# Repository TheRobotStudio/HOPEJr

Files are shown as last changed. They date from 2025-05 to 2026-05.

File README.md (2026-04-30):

# HOPEJr

## Repository Structure

### 📁 [`Humanoid/`](./Humanoid/) - Full Humanoid Development
*Original work by Rob Knight and updates for new motors, Robstride 02*

This directory contains the comprehensive humanoid robot development including:
- **Complete Body Design**: Full humanoid with arms, torso, and leg structures
- **URDF Models**: Complete robot descriptions for simulation

### 📁 [`Arm/`](./Arm/) - Hugging Face Integration & Teleoperation
*Latest work by Martino Russi at Hugging Face*

This directory contains the most recent development focused on:
- **LeRobot Integration**: Full software integration allowing recording, training, and inference
- **Teleoperation System**: Complete exoskeleton control system with 1:1 joint mapping
- **Simplified Assembly**: No soldering required, custom PCBs for easy connection
- **Enhanced Dexterity**: Improved finger design with underactuated DOF for better grasping

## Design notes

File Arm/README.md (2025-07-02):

# HOPEJr
HOPEJr is an open-source DIY Humanoid Robot with dexterous hands.

<div align="center">
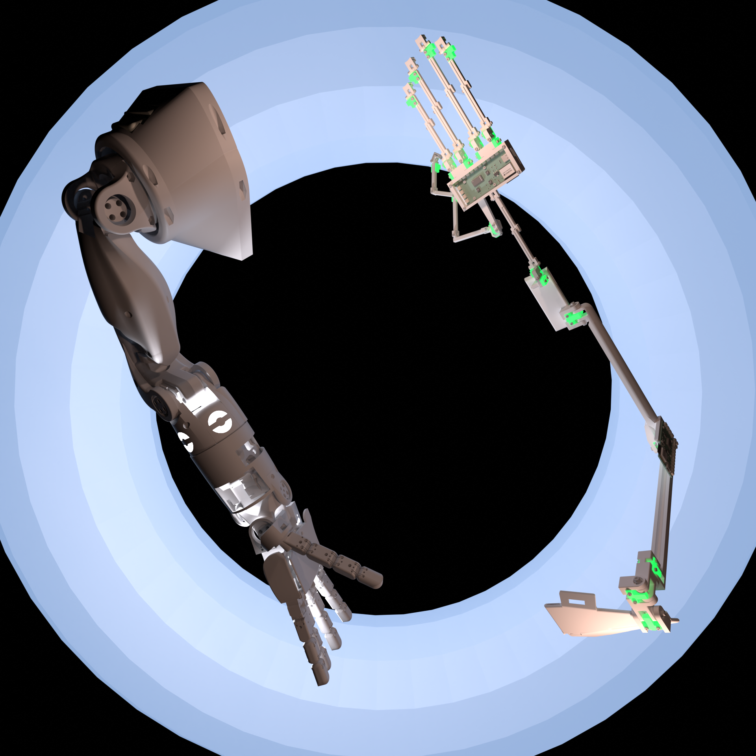
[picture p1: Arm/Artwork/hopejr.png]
HOPEJr Arm
  
</div>

As of 26/06/2025 the most up to date releases reflect the work of Martino Russi at Hugging Face. 
The repo now includes a teleoperation kit which builds on top of [Project Homunculus](https://github.com/nepyope/Project-Homunculus). STL for both can be found in 3dprint files/STL. STEP/arm.step and STEP/exoskeleton.step are the updated step files. PCBs are used to connect motors together and greatly simplify the assembly of the teleop exoskeleton.

# Improvements 

## Fingers
Fingers now have an additional, underactuated dof at the DIP joint. This allows the hand to adapt to the object being gripped. The build has been simplified, requiring much less physical strength. I addressed the core issue with rolling contact joints (subsceptibility to sheer and twist) by locking the wires into place using screws, using thicker fishing wire. I use 3d printer filament PTFE tubes to drive the tendons, simpler.
The thumb is now opposable: y approach for doing so was essentially modeling an actuated version of the thumb tracker i developed previously.
Spools were added to linearize the movement of the fingers relative to motor angle, allowing for faster action and 1:1 teleop

## Arm
Tolerances were relaxed slightly, and all threaded inserts were replaced with bolts. Including the PCBs this means that no soldering is required for the assembly. Wires can now pass behind the mantle, and the passive tendon has been removed, with the arm using a bulkier STS8215 to handle the extra load. 

## Exoskeleton
This teleop device has been developed specifically for HopeJr: each joint of the robot has a dual in the exoskeleton, including the hand. To measure angles we use diametric hall encoders, one for each joint of the hand and two for arm joints, allowing for more accurate tracking. This device is also fully assemblable without soldering, thanks to the custom PCBs that were developed at HF

## Software
All the above has been integrated with LeRobot, meaning it's now possible to record, train and do inference on HopeJr. 

---

> I want to foster a community that changes the world.
> 
> In a literal sense, the widespread adoption of robots is exactly that: the power to change the physical world with digital systems.
> 
> Open source has a crucial role to play in the development of this technology only if the tools are available to make that a practical reality for "the masses".
> 
> Open source software would clearly be a nonsense if they weren't billions of devices readily available for coding.
> 
> To this end, lowering cost whilst maintaining an adequate level of functionality is the highest design constraint.
> 
> The intention is to lever the tremendous performance increases that AI software offers to offset the significant differences in low cost hardware.
> 
> This is the great promise that needs testing: can AI genuinely control much lower cost hardware and finally produce the robots that we've all been dreaming of?
> 
> 3d printed plastic robots offer tremendous precision but significantly lower stiffness, a trait that is true in fact of all the lower cost versions of components in a robot. Here there may be a happy coincidence because the problem with expensive hardware is that it cannot be safely used around people. Industrial robots are made of metal and remarkably stiff gearboxes to produce rapid, highly precise movements - like a robot.
> 
> But people don't move that way, we are bouncy and capable of feats of strength and precision that far outperform an industrial machine of similar weight and power.
> 
> So, we know it's possible to learn how to control a bouncy system and we know they're lower cost.
> 
> All that's missing are the plans and instructions to build a DIY population of humanoid robots.

<div align="right"><em>- Rob Knight</em></div>

HOPEJr Community links:

WhatsApp: https://chat.whatsapp.com/HumZyAUoPps9EW8TwcGFkC

Discord: https://discord.gg/yPpf327PWF

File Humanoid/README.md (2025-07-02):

# HOPEJr
HOPEJr_open-source_DIY_Humanoid_Robot_with_dexterous_hands

As of 02/07/2025 the most up to date releases are for the Second_Arm_Draft(Addendum1) and the First_Hand_Draft.

Right arm: 3dprint_files/Second_Arm_Draft/Addendum1
Left Arm: 3dprint_files/Second_Arm_Draft/Left/Addendum1

When we do the first batch purchase of parts for a mass community build the Shoulder_Yaw, Shoulder_Roll and Elbow servos will also be upgraded to ST3250, same as the Shoulder_Pitch in the present design.

Addendum1 corrects the tendon pulley design at the elbow in the batch print trays.

The individual stl files of the new Elbow_Tendon_Hanger are included in case you have already printed the previous batch tray.

HL_Shoulder_Pitch_Mount_03b is also slightly changed and the files are included. They are now identical for left and right arms.



The HOPEJr hands are designed to maximise cost against performance with very small BOM's.

The BOM stands for the Bill of Materials which is a complete description of every component that is required to assemble the design. The real cost to build a robot can be much higher depending on how hard it is to arrange delivery of every last component in the BOM. Reducing BOM size has cumulative advantages at many levels and is one of the top design priorities now.

For the arms, it is recommended to use a higher performance servo in the shoulder pitch joint. This link is for 6 ST3215 and 1 ST3250 which is the 50kgcm version with steel gears:

https://www.alibaba.com/product-detail/1PC-ST3250-and-6PCS-12V-30KG_1601281510404.html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

This test of a finger structure replaces ball bearings with rolling joints that use the same size of fishing line as the tendons themselves (apologies that crimps are still required at this stage).

HOPEJr: Open-source, DIY, humanoid robots

I want to foster a community that changes the world.

In a literal sense, the widespread adoption of robots is exactly that: the power to change the physical world with digital systems.

HOPEJr Community link:

https://chat.whatsapp.com/HumZyAUoPps9EW8TwcGFkC

I want to foster a community that changes the world.

In a literal sense, the widespread adoption of robots is exactly that: the power to change the physical world with digital systems.

Open source has a crucial role to play in the development of this technology only if the tools are available to make that a practical reality for "the masses".

Open source software would clearly be a nonsense if they weren't billions of devices readily available for coding.

To this end, lowering cost whilst maintaining an adequate level of functionality is the highest design constraint.

The intention is to lever the tremendous performance increases that AI software offers to offset the significant differences in low cost hardware.

This is the great promise that needs testing: can AI genuinely control much lower cost hardware and finally produce the robots that we've all been dreaming of?

3d printed plastic robots offer tremendous precision but significantly lower stiffness, a trait that is true in fact of all the lower cost versions of components in a robot. Here there may be a happy coincidence because the problem with expensive hardware is that it cannot be safely used around people. Industrial robots are made of metal and remarkably stiff gearboxes to produce rapid, highly precise movements - like a robot.

But people don't move that way, we are bouncy and capable of feats of strength and precision that far outperform an industrial machine of similar weight and power.

So, we know it's possible to learn how to control a bouncy system and we know they're lower cost.

All that's missing are the plans and instructions to build a DIY population of humanoid robots.

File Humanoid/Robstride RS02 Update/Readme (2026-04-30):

30 April 2026 - Upload test stl for printing RS_SEA_Spring_Mount_05j_Motor_Mount.stl

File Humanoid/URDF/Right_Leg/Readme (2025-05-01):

Scroll down to robot.urdf

The zip is better organised and separates the meshes asstl files and the robot.urdf

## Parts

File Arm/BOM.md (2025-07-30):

BOM for HopeJr/Homunculus
========================

## HopeJr

### Motors:

| Model | Quantity | Reference | Details |
|---|---|---|---|
| SCS0009 Feetech | 16 | [Alibaba](https://www.alibaba.com/product-detail/High-Speed-6V-2-3KG-Micro_1601228126669.html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) | 3x fingers w\ thumb, 4x thumb (hand) |
| STS3250 Feetech | 2 | [Alibaba](https://www.alibaba.com/product-detail/12V-50KG-TTL-Brushless-HV-Waterproof_1601044995317.html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) | 1x shoulder yaw, 1x elbow flex (arm) |
| STS3215 Feetech 12V | 4 | [Alibaba](https://www.alibaba.com/product-detail/SOARM100-Robotic-Arm-12V-30KG-STS3215_1601216757543.html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) | arm |
| SM8512BL Feetech | 1 | [Alibaba](https://www.alibaba.com/product-detail/Feetech-12V-85kg-High-Torque-SM8512BL_1600728223869.html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) | shoulder pitch (arm) |

### Boards, power supplies and cables :

| Model | Specifications | Quantity  | References | Details 
|---|---|---|-|-|
| URT-1 board |  | 1 | [AliExpress](https://fr.aliexpress.com/item/1005008295936678.html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) | arm
| Waveshare servo driver board |  | 1  | [Amazon](https://amzn.eu/d/hYl6g60) [AliExpress](https://fr.aliexpress.com/item/1005006054189812.html?gatewayAdapt=glo2fra) | hand
| Power supply + DC adapter | 12V - 5A | 1 | [Amazon](https://amzn.eu/d/7MpnTSB) | arm
| Power supply | 5V - 4A | 1 | [Amazon](https://amzn.eu/d/9IXxrc8) | hand
| USB C &#8594; USB A cables | length : 3m | 2 | [Amazon](https://amzn.eu/d/5aKYcvO) | arm + hand

### Nuts & Bolts:

| Size | Item | Quantity | Reference | Details
|-|-|-|-|-
| M2 | screw set | 1 set | [Amazon](https://amzn.eu/d/cVf2toH) | hand
| M4 | nuts set | 1 set | [Amazon](https://www.amazon.fr/-/en/dp/B0D1V96WXT) | arm
|| 65mm screws | 6 | [Amazon](https://amzn.eu/d/41AhVIU) | 2x upper shoulder, 2x armpit, 2x wrist
|| 50mm screws | 1 |[Amazon](https://amzn.eu/d/8G91txy) | 1x hummeral
|| 45mm screws | 1 |[Amazon](https://amzn.eu/d/9xu0pLa) | 1x hummeral
|| 35mm screws | 1 |[Amazon](https://amzn.eu/d/c5xaClV) | 1x hummeral
|| 30mm screws | 3 |[Amazon](https://amzn.eu/d/7kudpAo) | 1x hummeral, 2x lower shoulder
|| 25mm screws | 1 |[Amazon](https://amzn.eu/d/2BEgJFc) | 1x upper elbow
| M6 | 35mm screws | 4 | [Amazon](https://amzn.eu/d/dzNhSkJ) | 2x elbow, 2x shoulder
|| spacers set | 1 set | [Amazon](https://www.amazon.fr/dp/B0D8H3M26T) | 2x elbow, 2x shoulder

### Bearings:

| Dimensions (width x inner diam. x outer diam.) | Quantity | Reference | Details
|-|-|-|-
| 10mm x 70mm x 90mm | 1 | [Amazon](https://amzn.eu/d/8Xz7m4C) | 1x wrist
| 50mm x 65mm x 7mm | 1 | [Amazon](https://amzn.eu/d/1xOo8re) | 1x shoulder
| 20mm x 27mm x 4mm | 18 | [Amazon](https://amzn.eu/d/9LXO205) | arm

### Springs: 

| Size (length x wire diam. x outer diam.) | Quantity | Reference | Details
|-|-|-|-
| 10mm x 0.3mm x 3mm | 1 set of 10 | [AliExpress](https://fr.aliexpress.com/item/4000250320601.html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) | 3x thumb, 2x fingers w\ thumb
| 15mm x 0.3mm x 2mm | 2 sets of 10 | [AliExpress](https://fr.aliexpress.com/item/4000250320601.html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) | 1x fingers w\ thumb

### Wire:

| Size (diameter x pound test) | Quafntity | Reference | Details
|-|-|-|-
|0.33 mm x 63 LB | 1 | [AliExpress](https://fr.aliexpress.com/item/1005002939956976.html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) | hand

### Miscallenous

|Item| Quantity | Reference | Details
|-|-|-|-
| PTFE tube | 1 | [Amazon](https://amzn.eu/d/fZaQyIG) | hand
| Finger protectors | 5 | [Amazon](https://amzn.eu/d/dV4cPsd) | 1x fingers

# Homunculus Teleop

## Screws

| Size | Item | Quantity | Reference 
|-|-|-|-
| M3 | screws set | 1 set | [Amazon](https://amzn.eu/d/io5NaX3)

## Bearings

| Size (width x inner diam. x outer diam.) | Quantity | Reference | Details
|-|-|-|-
| 6mm x 10mm x 3mm | 10 | [Amazon](https://amzn.eu/d/eKGj9gf) | 2x joint (upper arm)

## Velcro straps

| Size (width x length) | Quantity | Reference
|-|-|-
| 20mm x forearm diameter | 2 | [Amazon](https://a.co/d/8bawLVo)
| 20mm x shoulder diameter | 2 | [Amazon](https://a.co/d/8bawLVo)
| 20mm x half-torso diameter | 2 | [Amazon](https://a.co/d/8bawLVo)

## PCB
Create an account for [JLCPCB](https://jlcpcb.com/) and place an order. Add gerber file and select PCB assembly, in the next screen paste BOM and POS for teleop device and connectors

## Encoders

| Item | Specifications | Quantity | Reference | Details
|-|-|-|-|-
| Magnets |  diameter : 3mm | 23 | [Umagnets](https://www.umagnets.com/p/3mm-x-2mm-diametrically-magnetized-neodymium-disc-magnet-n38-small-powerful-rare-earth-round-magnets-for-craft/) |  1x joint
| SS49E linear hall sensors |  | 28 | [Amazon](https://amzn.eu/d/aemjs7f) | 1x joint (hand + wrist), 2x joint (upper arm)
| JSTS cables | 3 pins - length : 10cm | 1 set of 10 | [AliExpress](https://fr.aliexpress.com/item/1005007218127653.html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)
| | 3 pins, same direction - length : 15cm | 1 set of 10 | [AliExpress](https://fr.aliexpress.com/item/1005007218127653.html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)
| | 3 pins, same direction - length : 20cm | 2 sets of 10 | [AliExpress](https://fr.aliexpress.com/item/1005007218127653.html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)
| | 3 pins, same direction - length : 30cm | 1 set of 10 | [AliExpress](https://fr.aliexpress.com/item/1005007218127653.html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)

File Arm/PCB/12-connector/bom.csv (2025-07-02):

Designator | Footprint | Quantity | Value | LCSC Part #
J1, J10, J11, J12, J2, J3, J4, J5, J6, J7, J8, J9 | JST_EH_B3B-EH-A_1x03_P2.50mm_Vertical | 12 | JST_EH_B3B-EH-A_1x03_P2.50mm_Vertical

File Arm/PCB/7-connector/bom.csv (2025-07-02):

Designator | Footprint | Quantity | Value | LCSC Part #
J1, J2, J3, J4, J5, J6, J7 | JST | 7 | JST | C722693

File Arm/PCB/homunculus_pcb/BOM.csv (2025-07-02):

Designator | Footprint | Quantity | Value | LCSC Part #
C0, C1_13, C1_12, C1_11, C1_10, C1_9, C1_8, C1_7, C1_6, C1_5, C1_3, C1_2, C1, C2, C3_3, C9 | C0402 | 16 | C-0402-0.1uF-16V | C1525
C1_4, C2_2, C3_2, C3 | 0603 | 4 | 10µF
F1 | 0805 | 1 | Fuse_0805_2012Metric
H0, H1, H10, H11, H12, H13, H14, H15, H2, H3, H4, H5, H6, H7, H8, H9 | CONN-SMD_SM03B-SRSS-TB-LF-SN-P | 16 | JST-SM03B | C160403
J1 | USB_C_Receptacle_Palconn_UTC16-G | 1 | USB_C_Receptacle_USB2.0
R1, R4, R5, R6 | 0603 | 4 | 5.11K
R10_2, R10, R11, R12, R8 | 0603 | 5 | 10K
R3 | 0603 | 1 | 1M
R7 | 0603 | 1 | 1K
R9 | 0603 | 1 | 2.4K
U1 | ESP32-C3-WROOM-02 | 1 | ESP32-C3-WROOM-02
U2 | SOT-223-3_TabPin2 | 1 | AMS1117-3.3
U3 | SOIC-24_L15.4-W7.5-P1.27-LS10.3-BL | 1 | CD74HC4067M96 | C496123
U4, U5, U6 | SOIC-8_3.9x4.9mm_Pitch1.27mm | 3 | OPA340UA | C22365307

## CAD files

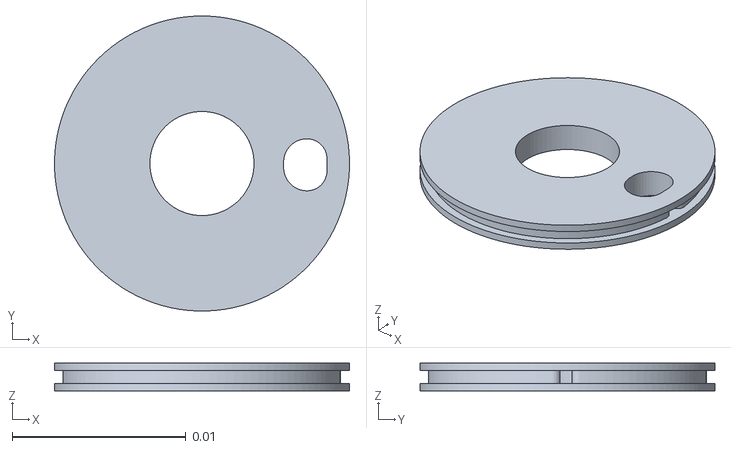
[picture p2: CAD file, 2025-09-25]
Arm/3dprint files/arm/spoolcover.stl
0.017 x 0.017 x 0.0016

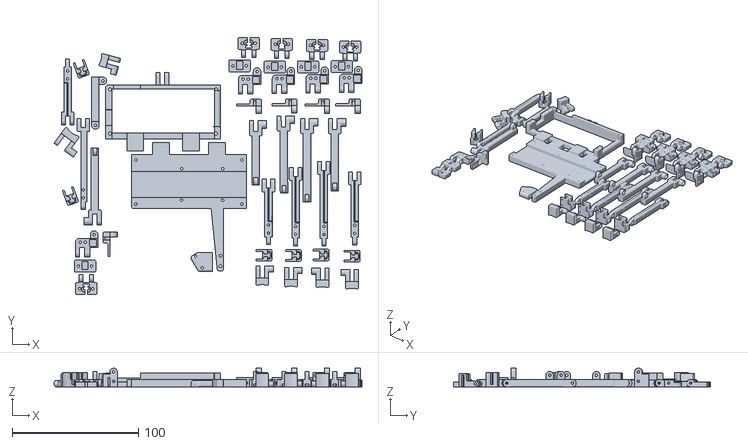
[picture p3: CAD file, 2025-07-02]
Arm/3dprint files/exoskeleton/left_glove.stl
243.9 x 203.8 x 14.8

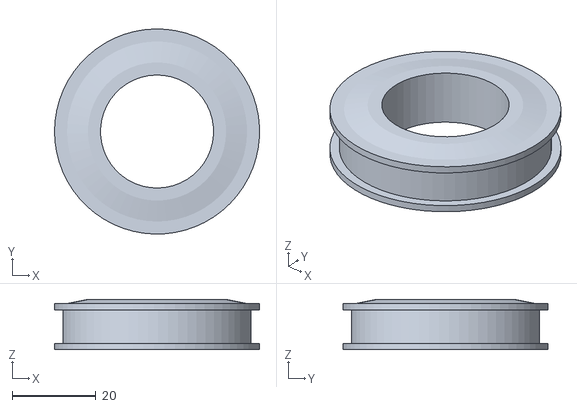
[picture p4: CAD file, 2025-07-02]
Humanoid/3dprint files/Arm_Test_01/Print_7DOF_8h_HL_02h_Pt_2 - HL_Elbow_Spool_01b-1.STL
49.0 x 49.0 x 12.0

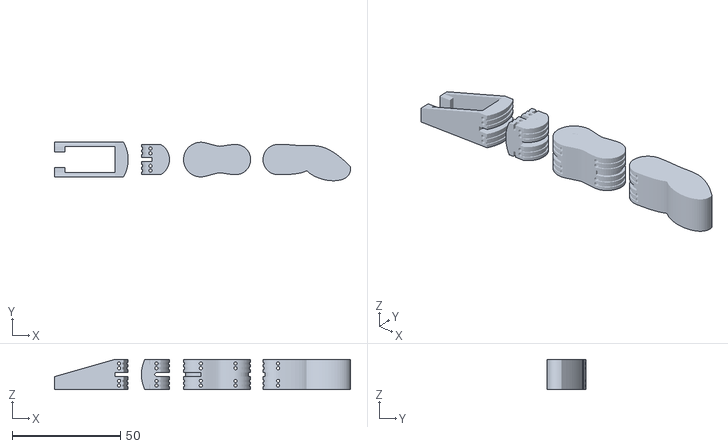
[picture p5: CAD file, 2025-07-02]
Humanoid/3dprint files/Finger_Test_01/Finger_Test_01.STL
136.6 x 17.8 x 14.0

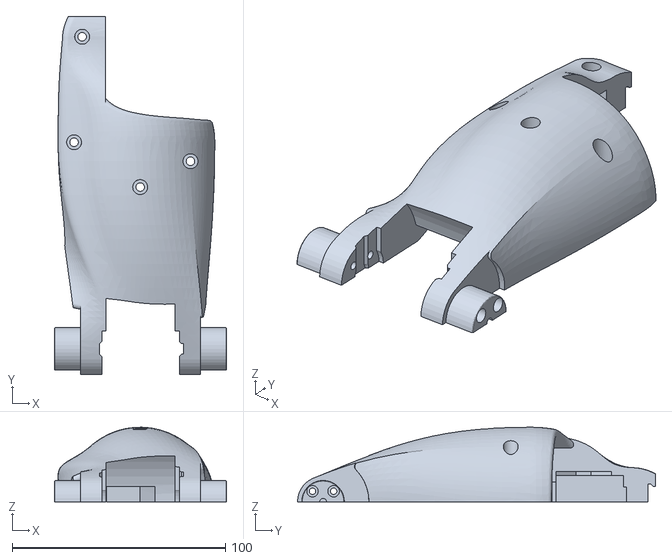
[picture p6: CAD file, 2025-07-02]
Humanoid/3dprint files/First_Arm_Draft/Parts_Print_7DOF_8h_HL_03f_Pt_1 - HL_Humeral_02n-2.STL
80.7 x 167.9 x 35.0

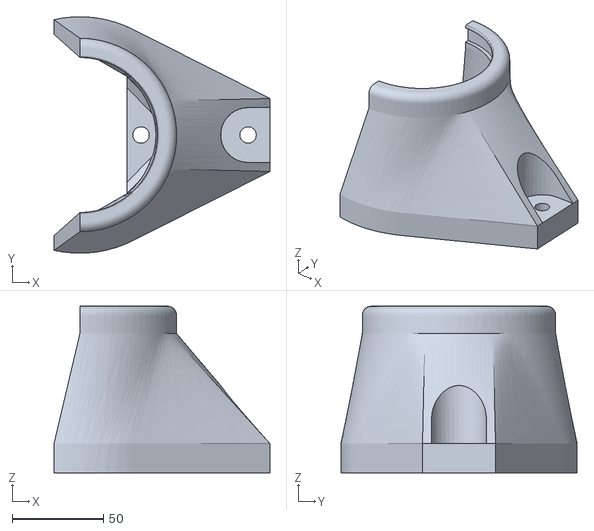
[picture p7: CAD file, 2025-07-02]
Humanoid/3dprint files/First_Draft_Torso/Print_Chest_01c.STL
118.4 x 129.5 x 91.4

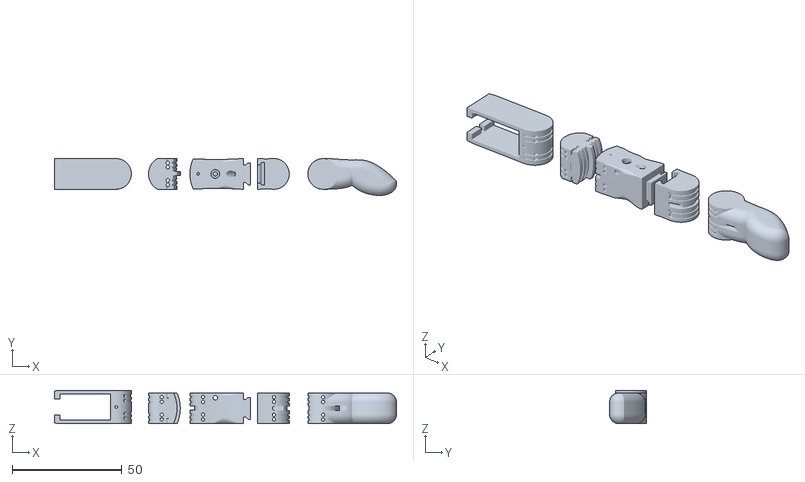
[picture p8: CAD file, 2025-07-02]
Humanoid/3dprint files/First_Finger_Draft/Print_HL_Finger_05d_Middle.STL
155.7 x 16.8 x 15.2

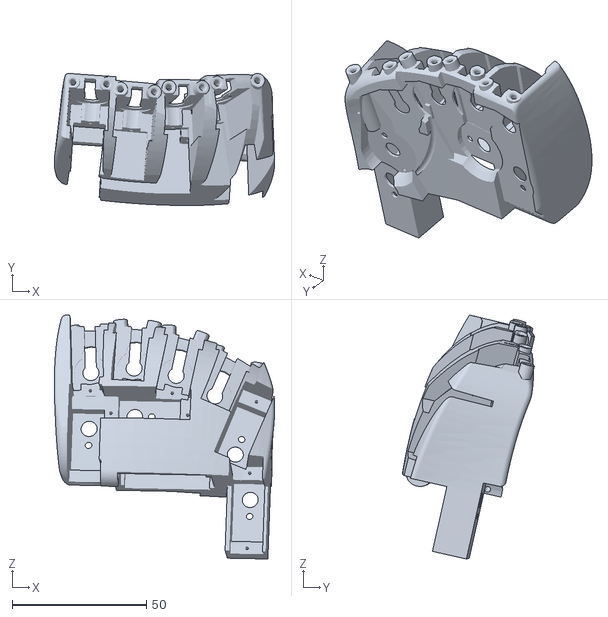
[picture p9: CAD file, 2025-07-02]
Humanoid/3dprint files/First_Hand_Draft/HopeLiteHand_05d_Part_Palm_01f.STL
82.1 x 49.2 x 90.9

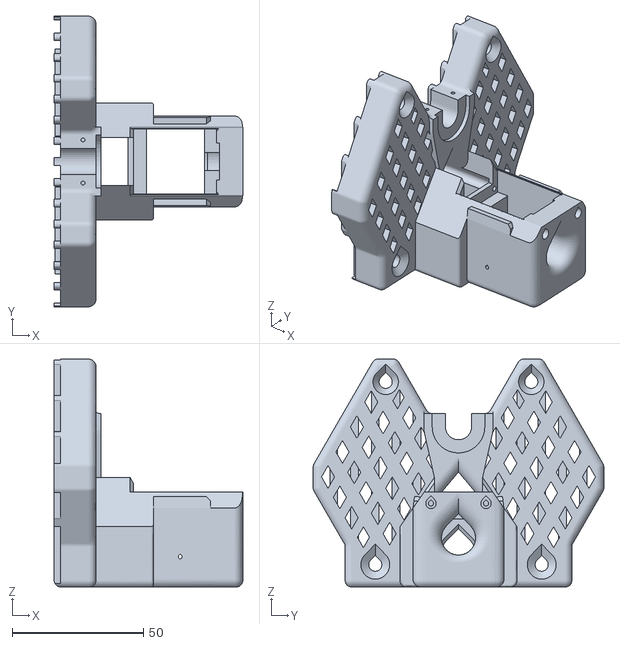
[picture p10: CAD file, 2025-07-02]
Humanoid/3dprint files/Second_Arm_Draft/Addendum1/HL_Shoulder_Pitch_Mount_03b_Bulk.STL
72.0 x 110.9 x 87.0

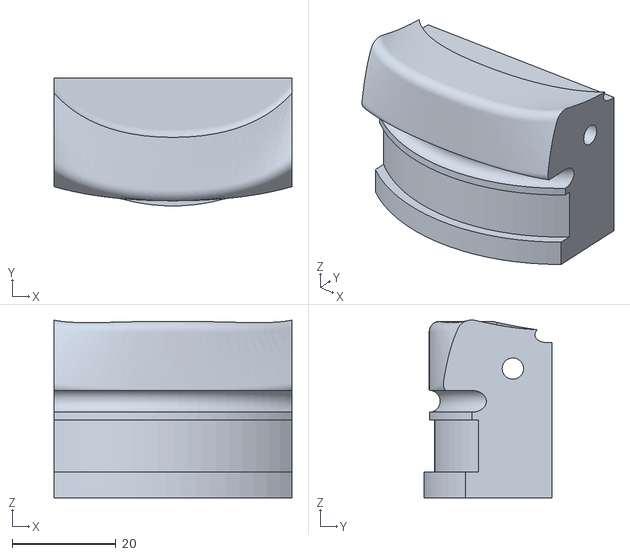
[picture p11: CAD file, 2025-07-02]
Humanoid/3dprint files/Second_Arm_Draft/Individual/Print_7DOF_8h_HL_03h_Pt_1 - HL_Shoulder_Pitch_Roller_Clip_02k-4.STL
45.8 x 24.6 x 34.2

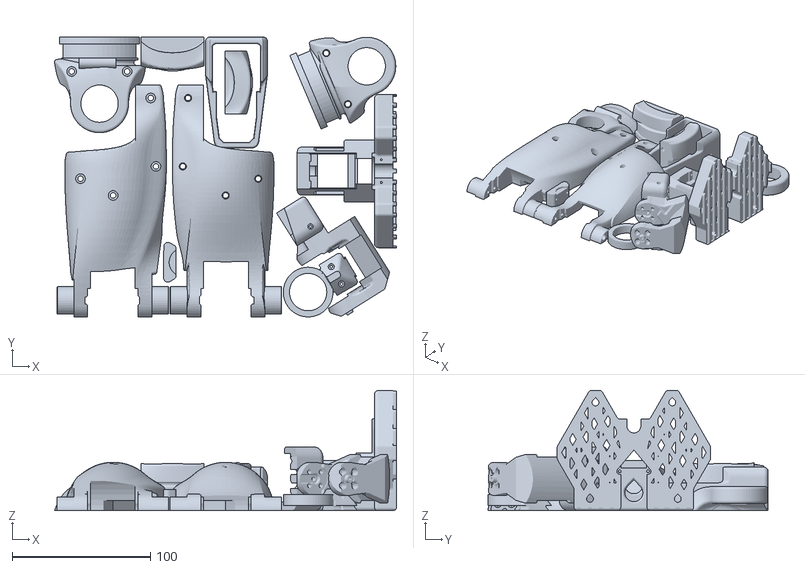
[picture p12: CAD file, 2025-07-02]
Humanoid/3dprint files/Second_Arm_Draft/Left/Addendum1/Print_7DOF_8h_HL_03i_Pt_1_Left.STL
247.4 x 202.5 x 87.0

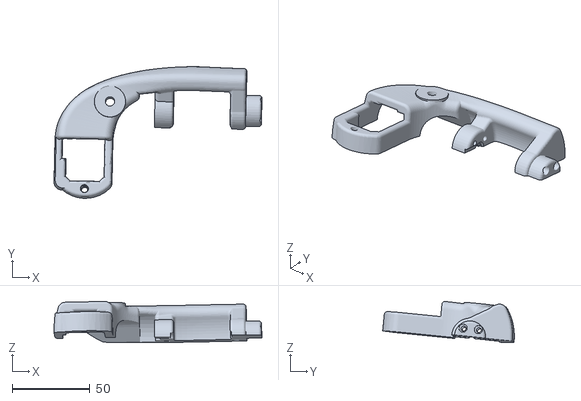
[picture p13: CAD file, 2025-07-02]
Humanoid/3dprint files/Second_Arm_Draft/Left/Individual/Print_7DOF_8h_HL_03h_Pt_2 - MirrorHL_Hum_Elbow_02q-5.STL
133.4 x 84.5 x 26.4

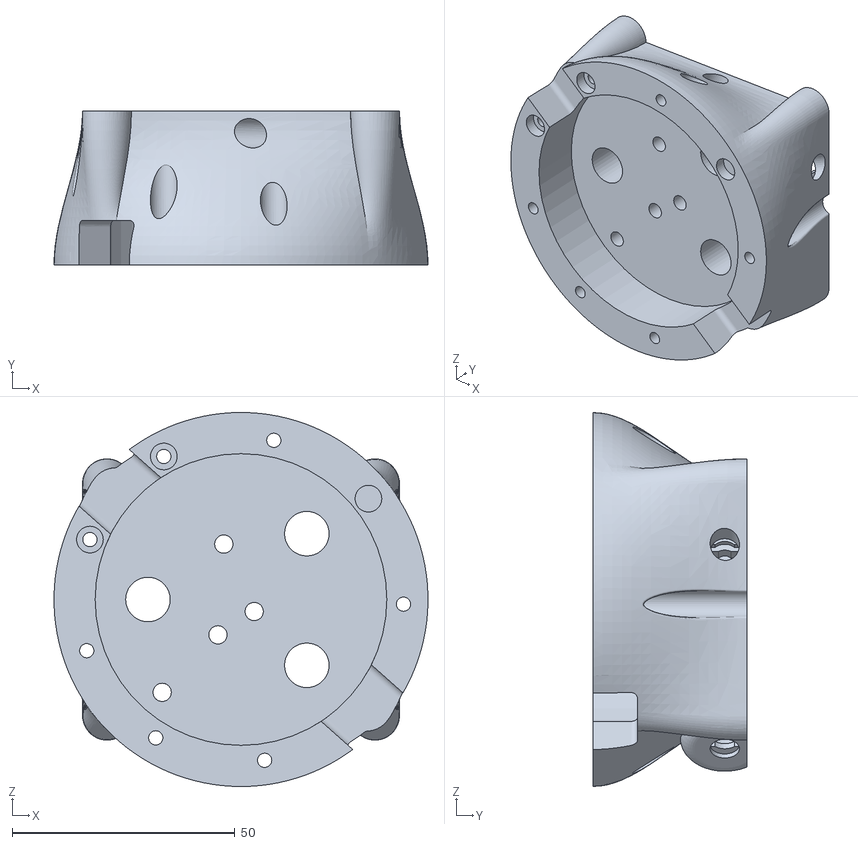
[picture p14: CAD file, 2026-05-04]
Humanoid/Robstride RS02 Update/RS_SEA_Spring_Mount_05j_Motor_Mount.STL
84.0 x 34.6 x 84.0

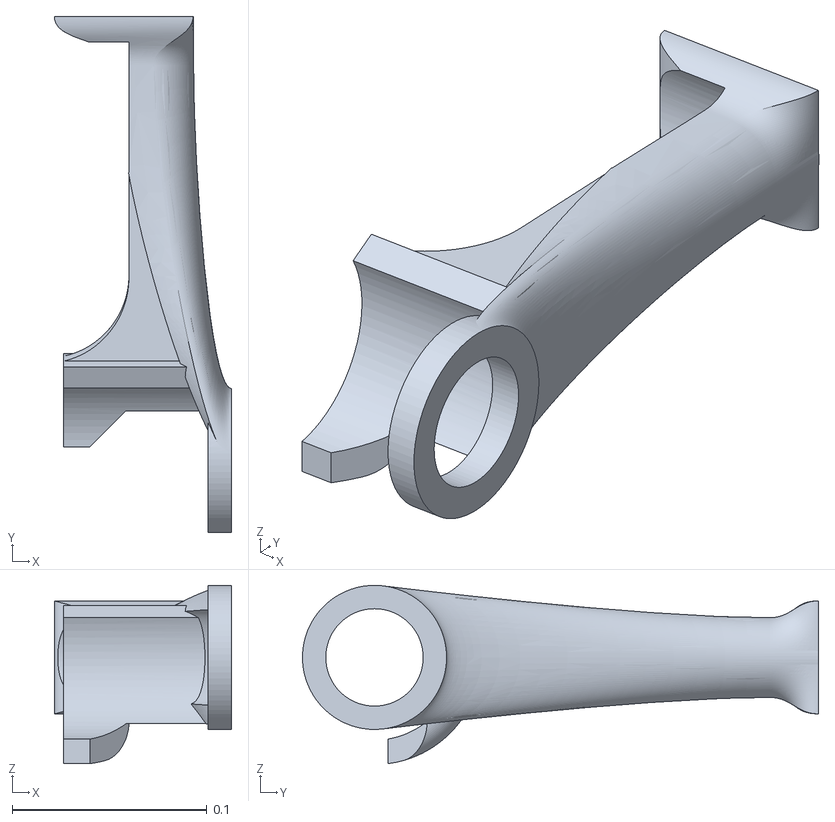
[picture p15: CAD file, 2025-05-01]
Humanoid/URDF/Right_Leg/sea_ankle_01g.stl
0.091 x 0.265 x 0.0915

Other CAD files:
Humanoid/3dprint files/Second_Arm_Draft/Left/Print_7DOF_8h_HL_03h_Pt_1_Left.STL
Humanoid/3dprint files/Second_Arm_Draft/Print_7DOF_8h_HL_03h_Pt_1.STL
Humanoid/STEP/HJr_Legs_07k.STEP
Arm/3dprint files/arm/left_forearm.stl
Arm/3dprint files/arm/left_humeral.stl
Arm/3dprint files/arm/left_shoulder.stl
Arm/3dprint files/arm/right_forearm.stl
Arm/3dprint files/arm/right_humeral.stl
Arm/3dprint files/arm/right_shoulder.stl
Arm/3dprint files/exoskeleton/left_exo.stl
Arm/3dprint files/exoskeleton/right_exo.stl
Arm/3dprint files/exoskeleton/right_glove.stl
Humanoid/3dprint files/Arm_Test_01/Print_7DOF_8h_HL_02h_Pt_1 - HL_Humeral_02m-1.STL
Humanoid/3dprint files/Arm_Test_01/Print_7DOF_8h_HL_02h_Pt_1 - HL_Humeral_02m-2.STL
Humanoid/3dprint files/Arm_Test_01/Print_7DOF_8h_HL_02h_Pt_1 - HL_Humeral_02m-3.STL
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

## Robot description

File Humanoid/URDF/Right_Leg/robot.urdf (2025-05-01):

<robot name="Hope_Right_Leg">
    <link name="world" />
    <link name="base_link">
        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
        <inertial>
            <origin xyz="-0.15922699731396347533 -0.013258650938079322851 0.14205554899684938452" />
            <mass value="1.2707541507968944661" />
            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
        </inertial>
        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
    </link>
    <link name="base_link_1">
        <inertial>
            <origin xyz="0 0 0" rpy="0 0 0" />
            <mass value="1e-9" />
            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
        </inertial>
        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
    </link>
    <joint name="base_link_1_fixing" type="fixed">
        <origin xyz="0 0 0" rpy="0 -0 0" />
        <parent link="base_link" />
        <child link="base_link_1" />
        <axis xyz="0 0 1" />
        <limit effort="1" velocity="20" />
        <joint_properties friction="0.0" />
    </joint>
    <link name="base_link_2">
        <inertial>
            <origin xyz="0 0 0" rpy="0 0 0" />
            <mass value="1e-9" />
            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
        </inertial>
        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
    </link>
    <joint name="base_link_2_fixing" type="fixed">
        <origin xyz="0 0 0" rpy="0 -0 0" />
        <parent link="base_link" />
        <child link="base_link_2" />
        <axis xyz="0 0 1" />
        <limit effort="1" velocity="20" />
        <joint_properties friction="0.0" />
    </joint>
    <link name="base_link_3">
        <inertial>
            <origin xyz="0 0 0" rpy="0 0 0" />
            <mass value="1e-9" />
            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
        </inertial>
        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
    </link>
    <joint name="base_link_3_fixing" type="fixed">
        <origin xyz="0 0 0" rpy="0 -0 0" />
        <parent link="base_link" />
        <child link="base_link_3" />
        <axis xyz="0 0 1" />
        <limit effort="1" velocity="20" />
        <joint_properties friction="0.0" />
    </joint>
    <link name="base_link_4">
        <inertial>
            <origin xyz="0 0 0" rpy="0 0 0" />
            <mass value="1e-9" />
            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
        </inertial>
        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
    </link>
    <joint name="base_link_4_fixing" type="fixed">
        <origin xyz="0 0 0" rpy="0 -0 0" />
        <parent link="base_link" />
        <child link="base_link_4" />
        <axis xyz="0 0 1" />
        <limit effort="1" velocity="20" />
        <joint_properties friction="0.0" />
    </joint>
    <link name="base_link_5">
        <inertial>
            <origin xyz="0 0 0" rpy="0 0 0" />
            <mass value="1e-9" />
            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
        </inertial>
        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
    </link>
    <joint name="base_link_5_fixing" type="fixed">
        <origin xyz="0 0 0" rpy="0 -0 0" />
        <parent link="base_link" />
        <child link="base_link_5" />
        <axis xyz="0 0 1" />
        <limit effort="1" velocity="20" />
        <joint_properties friction="0.0" />
    </joint>
    <link name="base_link_6">
        <inertial>
            <origin xyz="0 0 0" rpy="0 0 0" />
            <mass value="1e-9" />
            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
        </inertial>
        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
    </link>
    <joint name="base_link_6_fixing" type="fixed">
        <origin xyz="0 0 0" rpy="0 -0 0" />
        <parent link="base_link" />
        <child link="base_link_6" />
        <axis xyz="0 0 1" />
        <limit effort="1" velocity="20" />
        <joint_properties friction="0.0" />
    </joint>
    <link name="base_link_7">
        <inertial>
            <origin xyz="0 0 0" rpy="0 0 0" />
            <mass value="1e-9" />
            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
        </inertial>
        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
    </link>
    <joint name="base_link_7_fixing" type="fixed">
        <origin xyz="0 0 0" rpy="0 -0 0" />
        <parent link="base_link" />
        <child link="base_link_7" />
        <axis xyz="0 0 1" />
        <limit effort="1" velocity="20" />
        <joint_properties friction="0.0" />
    </joint>
    <link name="base_link_8">
        <inertial>
            <origin xyz="0 0 0" rpy="0 0 0" />
            <mass value="1e-9" />
            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
        </inertial>
        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
    </link>
    <joint name="base_link_8_fixing" type="fixed">
        <origin xyz="0 0 0" rpy="0 -0 0" />
        <parent link="base_link" />
        <child link="base_link_8" />
        <axis xyz="0 0 1" />
        <limit effort="1" velocity="20" />
        <joint_properties friction="0.0" />
    </joint>
    <link name="base_link_9">
        <inertial>
            <origin xyz="0 0 0" rpy="0 0 0" />
            <mass value="1e-9" />
            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
        </inertial>
        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
    </link>
    <joint name="base_link_9_fixing" type="fixed">
        <origin xyz="0 0 0" rpy="0 -0 0" />
        <parent link="base_link" />
        <child link="base_link_9" />
        <axis xyz="0 0 1" />
        <limit effort="1" velocity="20" />
        <joint_properties friction="0.0" />
    </joint>
    <link name="base_link_10">
        <inertial>
            <origin xyz="0 0 0" rpy="0 0 0" />
            <mass value="1e-9" />
            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
        </inertial>
        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
    </link>
    <joint name="base_link_10_fixing" type="fixed">
        <origin xyz="0 0 0" rpy="0 -0 0" />
        <parent link="base_link" />
        <child link="base_link_10" />
        <axis xyz="0 0 1" />
        <limit effort="1" velocity="20" />
        <joint_properties friction="0.0" />
    </joint>
    <link name="base_link_11">
        <inertial>
            <origin xyz="0 0 0" rpy="0 0 0" />
            <mass value="1e-9" />
            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
        </inertial>
        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
    </link>
    <joint name="base_link_11_fixing" type="fixed">
        <origin xyz="0 0 0" rpy="0 -0 0" />
        <parent link="base_link" />
        <child link="base_link_11" />
        <axis xyz="0 0 1" />
        <limit effort="1" velocity="20" />
        <joint_properties friction="0.0" />
    </joint>
    <link name="base_link_12">
        <inertial>
            <origin xyz="0 0 0" rpy="0 0 0" />
            <mass value="1e-9" />
            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
        </inertial>
        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
    </link>
    <joint name="base_link_12_fixing" type="fixed">
        <origin xyz="0 0 0" rpy="0 -0 0" />
        <parent link="base_link" />
        <child link="base_link_12" />
        <axis xyz="0 0 1" />
        <limit effort="1" velocity="20" />
        <joint_properties friction="0.0" />
    </joint>
    <link name="base_link_13">
        <inertial>
            <origin xyz="0 0 0" rpy="0 0 0" />
            <mass value="1e-9" />
            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
        </inertial>
        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
    </link>
    <joint name="base_link_13_fixing" type="fixed">
        <origin xyz="0 0 0" rpy="0 -0 0" />
        <parent link="base_link" />
        <child link="base_link_13" />
        <axis xyz="0 0 1" />
        <limit effort="1" velocity="20" />
        <joint_properties friction="0.0" />
    </joint>
    <link name="base_link_14">
        <inertial>
            <origin xyz="0 0 0" rpy="0 0 0" />
            <mass value="1e-9" />
            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
        </inertial>
        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
    </link>
    <joint name="base_link_14_fixing" type="fixed">
        <origin xyz="0 0 0" rpy="0 -0 0" />
        <parent link="base_link" />
        <child link="base_link_14" />
        <axis xyz="0 0 1" />
        <limit effort="1" velocity="20" />
        <joint_properties friction="0.0" />
    </joint>
    <link name="base_link_15">
        <inertial>
            <origin xyz="0 0 0" rpy="0 0 0" />
            <mass value="1e-9" />
            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
        </inertial>
        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
    </link>
    <joint name="base_link_15_fixing" type="fixed">
        <origin xyz="0 0 0" rpy="0 -0 0" />
        <parent link="base_link" />
        <child link="base_link_15" />
        <axis xyz="0 0 1" />
        <limit effort="1" velocity="20" />
        <joint_properties friction="0.0" />
    </joint>
    <link name="base_link_16">
        <inertial>
            <origin xyz="0 0 0" rpy="0 0 0" />
            <mass value="1e-9" />
            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
        </inertial>
        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
    </link>
    <joint name="base_link_16_fixing" type="fixed">
        <origin xyz="0 0 0" rpy="0 -0 0" />
        <parent link="base_link" />
        <child link="base_link_16" />
        <axis xyz="0 0 1" />
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

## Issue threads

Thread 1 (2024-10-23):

What is "high strength tendon motor tbd" in BOM?

Palladiumm, 2024-10-23:
Firstly, I'm grateful for everything you've done. Your projects are amazing.
Secondly - I have a question: What is "high strength tendon motor tbd" in BOM?
Could you bring an example of this part?

bandirevanth, 2025-05-31:
In a Bill of Materials (BOM), the entry "high-strength tendon motor TBD" generally refers to a motorised actuator system designed to pull or control high-strength tendons like cables, usually in robotics, prosthetics, or biomechanical systems.  The final motor part is yet to be selected (TBD).

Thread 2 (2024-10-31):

BOM - link to parts

rraymakers, 2024-10-31:
I would suggest to update the BOMs with affiliated links where people can buy the parts.
This will make it easier to find the correct parts and it gives the project some income to continue.

TheRobotStudio, 2024-10-31:
Yes, links will go up today

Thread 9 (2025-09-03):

Request: PCB purchase link and assembly video for HOPEJr

ZhangWuWei, 2025-09-03:
Hi there, thanks a ton for open-sourcing HOPEJr — it’s an awesome project!

I was wondering if you could share:
	1.	A purchase link for the HOPEJr PCB board (if available).
	2.	A full assembly video/tutorial for the robotic arm.

This would be super helpful for anyone trying to replicate the project.
Really appreciate your support! 🙏

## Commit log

2024-12-28 Update BOM
2025-01-09 Create BOM
    Everything I can think of.
    That's not a guarantee of completeness.
2025-01-09 Top half of the chest enclosure
    The chest gives important support to the main shoulder pitch bearing and is essential for any activities beyond light testing of the arm.
    [Mantle_01a.STL]
2025-01-09 Update Mantle and set orientation for printing.
    [Mantle_01a.STL, Print_Mantle_01c.STL]
2025-02-19 Upload URDF Overall_01b.SLDAM.zip
2025-02-19 Create URDF folder
2025-02-19 Upload test URDF
    Overall_01b: Test URDF with right leg and Pelvis
2025-02-19 Upload URDF with two legs
    Overall_01d: Two legs and pelvis, Some of the axis may be flipped.
2025-05-01 Scroll down to robot.urdf
    Scroll down to robot.urdf
    [45x58x7.stl, 4x7x2.5_10.stl, 70x90x10.stl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]
2025-07-02 Create SW2018 CAD
2025-07-02 add separate Humanoid and Arm sections
    [45x58x7.stl, 4x7x2.5_10.stl, 70x90x10.stl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]
2025-07-09 Add HopeJR STEP & archive
    [HJr_Legs_07k.STEP]
2025-07-11 separate hand from arm
2025-07-30 update motors product link
2025-07-30 Update motors list
2025-08-11 add wrist holders to forearm stl
2025-09-25 add scs spool
    [spoolcover.stl]
2025-10-06 update exo code
    Each joint now has a `flipped[]` flag that, when true, mirrors both sin and cos readings
    (4095 - value) before computing atan2. This preserves 90° phase alignment while allowing
    the ±π discontinuity to be shifted outside the joint’s physical range.
2026-05-04 Update stl with clearances
    [RS_SEA_Spring_Mount_05j_Motor_Mount.STL]
